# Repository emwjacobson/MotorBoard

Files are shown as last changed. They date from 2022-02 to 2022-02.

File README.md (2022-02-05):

# MotorBoard

Goals for this project:

- Integreate ESP32
- Control up to 3 stepper motors
  - Shared pins:
    - MS1, MS2, MS3, Reset, Enable
  - Unique pins per stepper:
    - Sleep, Step, Dir
  - Total of 5 + 3(3) = 14 pins to control 3 steppers.
- Control up to 2 "hobby" servos
- 6 digital inputs
  - Limit switches, User IO (Buttons)

Decisions that need to be made:
- How will it be powered?
  - Barrel Jack? Screw Terminals?
  - Stepper motors will run off 8-35V, so 12V input should be good
- Stepper Connector
  - Leaning towards screw terminals, as they seem pretty universal
  - Could also use 4/6-pin JST connector
- Should step resolution be software controlled, or have jumpers on PCB?

Components:
- [Stepper Driver](https://www.lcsc.com/product-detail/Motor-Driver-ICs_Allegro-MicroSystems-LLC-A4988SETTR-T_C38437.html)
- [ESP32 Module](https://www.lcsc.com/product-detail/WiFi-Modules_Espressif-Systems-ESP32-WROVER-IE-8MB_C2934565.html)
  - The IE(8MB) seems to be the cheapest in the WROVER-IE series. The 4MB and 16MB variants are also supported, though seem slightly more expensive on LCSC
  - The WROVER-E series is also supported. The only difference between the two is the resistor connecting the antenna output either to the PCB antenna, or the external antenna. The -E model attaches to the PCB antenna, and the -IE model attaches to the external antenna.

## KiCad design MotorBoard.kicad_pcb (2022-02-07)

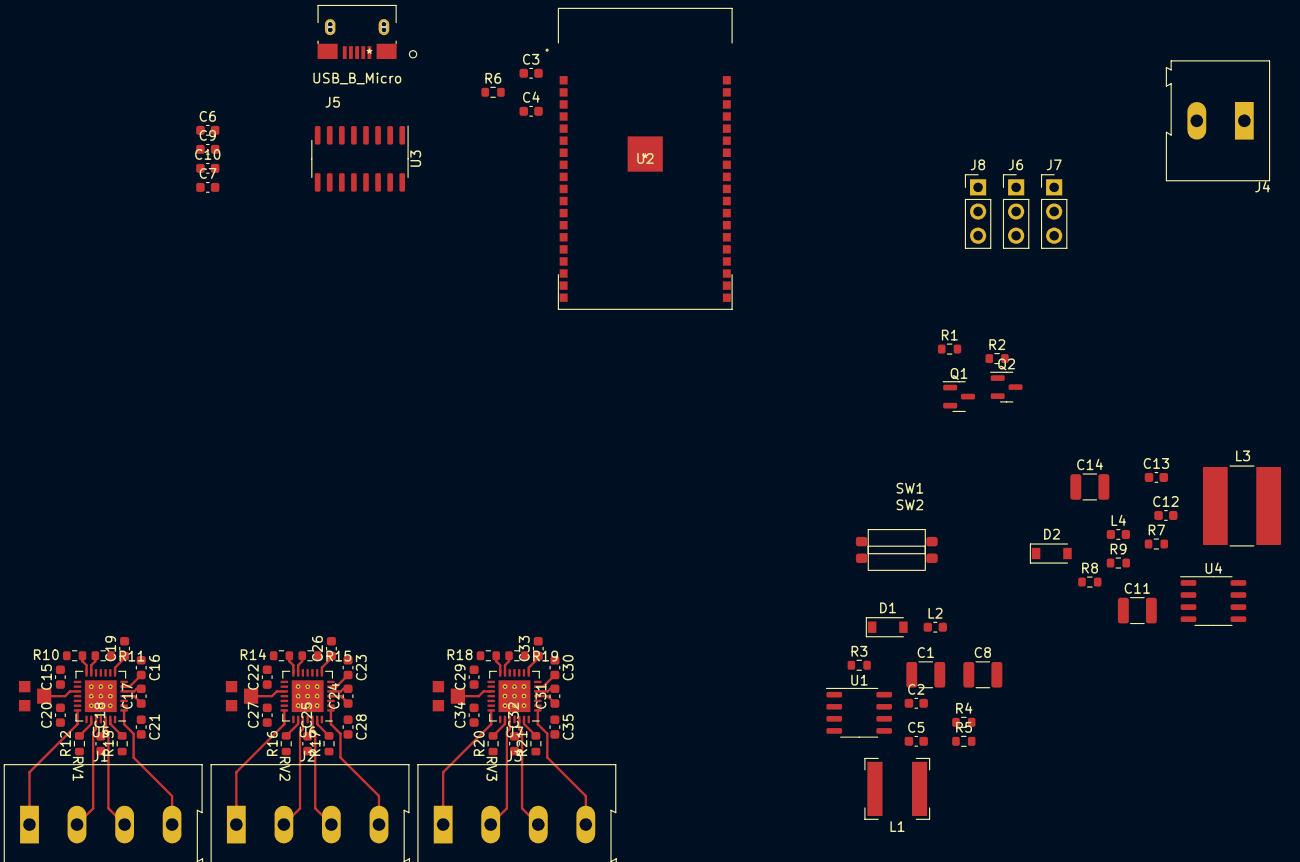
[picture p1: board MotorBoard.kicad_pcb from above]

Board: 4 copper layers, 84 parts (0 on the bottom side), 79 nets.

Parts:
C1, C8, C11, C14: 100uF; C_1210_3225Metric
C2: 150pF; C_0603_1608Metric
C3: 22uF; C_0603_1608Metric
C4, C7, C9, C10, C16, C17, C20, C21, C23, C24, C27, C28, C30, C31, C34, C35: 100nF; C_0603_1608Metric
C5, C6, C13: 10uF; C_0603_1608Metric
C12: 200pF; C_0603_1608Metric
C15, C19, C22, C26, C29, C33: 220nF; C_0603_1608Metric
C18, C25, C32: 4.7uF; C_0603_1608Metric
D1, D2: 1N5819; D_SOD-123
J1, J2, J3: Screw_Terminal_01x04; TerminalBlock_Altech_AK300-4_P5.00mm
J4: Screw_Terminal_01x02; TerminalBlock_Altech_AK300-2_P5.00mm
J5: USB_B_Micro; U254-051T-4BH83-S1S
J6, J7, J8: Conn_01x03; PinHeader_1x03_P2.54mm_Vertical
L1: 33uH; L_Bourns-SRN6028
L2, L4: 1uH; L_0603_1608Metric
L3: 47uH; L_Bourns-SRN8040_8x8.15mm
Q1, Q2: Q_NPN_BEC; SOT-23
R1, R2, R6, R11, R15, R19: 10k; R_0603_1608Metric
R3: 0.39; R_0603_1608Metric
R4: 18k; R_0603_1608Metric
R5: 11k; R_0603_1608Metric
R7: 0.5; R_0603_1608Metric
R8: 3k; R_0603_1608Metric
R9: 1k; R_0603_1608Metric
R10, R14, R18: 100k; R_0603_1608Metric
R12, R13, R16, R17, R20, R21: 0.05; R_0603_1608Metric
RV1, RV2, RV3: 4.7k; VG039NCHXTB472
SW1, SW2: SW_SPST; TS-1101-C-W
U1, U4: MC34063AD; SOP-8_3.9x4.9mm_P1.27mm
U2: ESP32-WROVER-E; ESP32-WROVER-IE
U3: CH340C; SOIC-16_3.9x9.9mm_P1.27mm
U5, U6, U7: A4988SETTR-T; QFN-28-1EP_5x5mm_P0.5mm_EP3.35x3.35mm_ThermalVias

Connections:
3v3: C3.1, C4.1, C8.1, L2.2, Q1.3 (C), R6.1, SW1.1 (A), U2.2 (3V3)
5v: C14.1, C15.1, C22.1, C29.1, J6.1, J7.1, J8.1, L4.2, R10.2, R14.2, R18.2, RV1.1, RV2.1, RV3.1, U5.15 (VDD), U6.15 (VDD), U7.15 (VDD)
12v: C1.1, C11.1, C16.1, C18.1, C20.1, C21.1, C23.1, C25.1, C27.1, C28.1, C30.1, C32.1, C34.1, C35.1, J4.1, R3.1, R7.1, U1.6 (Vin), U4.6 (Vin), U5.22 (VBB1), U5.28 (VBB2), U6.22 (VBB1), U6.28 (VBB2), U7.22 (VBB1), U7.28 (VBB2)
/BOOT: Q2.3 (C), SW2.1 (A), U2.25 (IO0)
/DTR: Q1.2 (E), R2.1, U3.14 (~RTS)
/ESP_RX: U2.34 (RXD0), U3.2 (TXD)
/ESP_TX: U2.35 (TXD0), U3.3 (RXD)
/RTS: Q2.2 (E), R1.1, U3.13 (~DTR)
/SERVO1: J7.2, U2.11 (IO26)
/SERVO2: J8.2, U2.12 (IO27)
/SERVO3: J6.2, U2.13 (IO14)
/ST1_1A: J1.2, U5.24 (OUT1A)
/ST1_1B: J1.1, U5.21 (OUT1B)
/ST1_2A: J1.3, U5.26 (OUT2A)
/ST1_2B: J1.4, U5.1 (OUT2B)
/ST1_DIR: U2.26 (IO4), U5.19 (DIR)
/ST1_STEP: U2.29 (IO5), U5.16 (STEP)
/ST2_1A: J2.2, U6.24 (OUT1A)
/ST2_1B: J2.1, U6.21 (OUT1B)
/ST2_2A: J2.3, U6.26 (OUT2A)
/ST2_2B: J2.4, U6.1 (OUT2B)
/ST2_DIR: U2.23 (IO15), U6.19 (DIR)
/ST2_STEP: U2.24 (IO2), U6.16 (STEP)
/ST3_1A: J3.2, U7.24 (OUT1A)
/ST3_1B: J3.1, U7.21 (OUT1B)
/ST3_2A: J3.3, U7.26 (OUT2A)
/ST3_2B: J3.4, U7.1 (OUT2B)
/ST3_DIR: U2.14 (IO12), U7.19 (DIR)
/ST3_STEP: U2.16 (IO13), U7.16 (STEP)
/ST_Enable: U2.31 (IO19), U5.2 (~ENABLE), U6.2 (~ENABLE), U7.2 (~ENABLE)
/ST_MS1: U2.37 (IO23), U5.9 (MS1), U6.9 (MS1), U7.9 (MS1)
/ST_MS2: U2.36 (IO22), U5.10 (MS2), U6.10 (MS2), U7.10 (MS2)
/ST_MS3: U2.33 (IO21), U5.11 (MS3), U6.11 (MS3), U7.11 (MS3)
/ST_Reset: U2.30 (IO18), U5.12 (RESET), U6.12 (RESET), U7.12 (RESET)
/USB_5v: C6.1, C7.1, C9.1, J5.1 (VBUS), U3.16 (VCC)
/USB_D+: J5.3 (D+), U3.5 (UD+)
/USB_D-: J5.2 (D-), U3.6 (UD-)
GND: C1.2, C2.2, C3.2, C4.2, C5.2, C6.2, C7.2, C8.2, C9.2, C10.2, C11.2, C12.2, C13.2, C14.2, C15.2, C18.2, C19.2, C20.2, C21.2, C22.2, C25.2, C26.2, C27.2, C28.2, C29.2, C32.2, C33.2, C34.2, C35.2, D1.2 (A), D2.2 (A), J4.2, J5.5 (GND), J6.3, J7.3, J8.3, R5.2, R9.2, R11.2, R12.1, R13.1, R15.2, R16.1, R17.1, R19.2, R20.1, R21.1, RV1.3, RV2.3, RV3.3, SW1.2 (B), SW2.2 (B), U1.4 (GND), U2.1 (GND), U2.15 (GND), U2.38 (GND), U2.39 (GND), U3.1 (GND), U4.4 (GND), U5.3 (GND), U5.18 (GND), U5.29 (GND), U6.3 (GND), U6.18 (GND), U6.29 (GND), U7.3 (GND), U7.18 (GND), U7.29 (GND)
unnamed: C2.1, U1.3 (TC)
unnamed: C5.1, L1.2, L2.1, R4.1
unnamed: C10.1, U3.4 (V3)
unnamed: C12.1, U4.3 (TC)
unnamed: C13.1, L3.2, L4.1, R8.1
unnamed: C16.2, U5.6 (VCP)
unnamed: C17.1, U5.4 (CP1)
unnamed: C17.2, U5.5 (CP2)
unnamed: C19.1, U5.8 (VREG)
unnamed: C23.2, U6.6 (VCP)
unnamed: C24.1, U6.4 (CP1)
unnamed: C24.2, U6.5 (CP2)
unnamed: C26.1, U6.8 (VREG)
unnamed: C30.2, U7.6 (VCP)
unnamed: C31.1, U7.4 (CP1)
unnamed: C31.2, U7.5 (CP2)
unnamed: C33.1, U7.8 (VREG)
unnamed: D1.1 (K), L1.1, U1.2 (SwE)
unnamed: D2.1 (K), L3.1, U4.2 (SwE)
unnamed: Q1.1 (B), R1.2
unnamed: Q2.1 (B), R2.2
unnamed: R3.2, U1.1 (SwC), U1.7 (Ipk), U1.8 (DC)
unnamed: R4.2, R5.1, U1.5 (Vfb)
unnamed: R6.2, U2.3 (EN)
unnamed: R7.2, U4.1 (SwC), U4.7 (Ipk), U4.8 (DC)
unnamed: R8.2, R9.1, U4.5 (Vfb)
unnamed: R10.1, U5.14 (~SLEEP)
unnamed: R11.1, U5.13 (ROSC)
unnamed: R12.2, U5.23 (SENSE1)
unnamed: R13.2, U5.27 (SENSE2)
unnamed: R14.1, U6.14 (~SLEEP)
unnamed: R15.1, U6.13 (ROSC)
unnamed: R16.2, U6.23 (SENSE1)
unnamed: R17.2, U6.27 (SENSE2)
unnamed: R18.1, U7.14 (~SLEEP)
unnamed: R19.1, U7.13 (ROSC)
unnamed: R20.2, U7.23 (SENSE1)
unnamed: R21.2, U7.27 (SENSE2)
unnamed: RV1.2, U5.17 (VREF)
unnamed: RV2.2, U6.17 (VREF)
unnamed: RV3.2, U7.17 (VREF)

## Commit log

2022-02-05 Began work on schematic
    [MotorBoard.kicad_sch]
2022-02-05 Wired stepper driver and power supply section
    [MotorBoard.kicad_sch, PowerSupply.kicad_sch]
2022-02-06 Broke stepper drivers into hierarchial sheets
    [MotorBoard.kicad_sch, StepperDriver.kicad_sch]
2022-02-06 Added part numbers to majority of components
    [MotorBoard.kicad_sch, StepperDriver.kicad_sch]
2022-02-06 Started assigning footprints
    [MotorBoard.kicad_sch, StepperDriver.kicad_sch]
2022-02-06 Added servo headers
    [MotorBoard.kicad_sch, StepperDriver.kicad_sch]
2022-02-07 Began work on PCB layout
    [MotorBoard.kicad_pcb, MotorBoard.kicad_sch, StepperDriver.kicad_sch]
